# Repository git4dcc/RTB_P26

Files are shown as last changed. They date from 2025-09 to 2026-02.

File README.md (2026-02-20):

# RTB_P26




This is a **motor DCC decoder development board** you can plug right into a breadboard. It has all the necessary hardware for a DCC decoder, except for the microcontroller.

<details>
<summary>See also</summary>

- [RTB_D16](/../../../../git4dcc/RTB_D16) (DCC Decoder)

</details>

<details>
<summary>User Guides</summary>

- User Guide - DE (to be done)
- User Guide - EN (to be done)

</details>

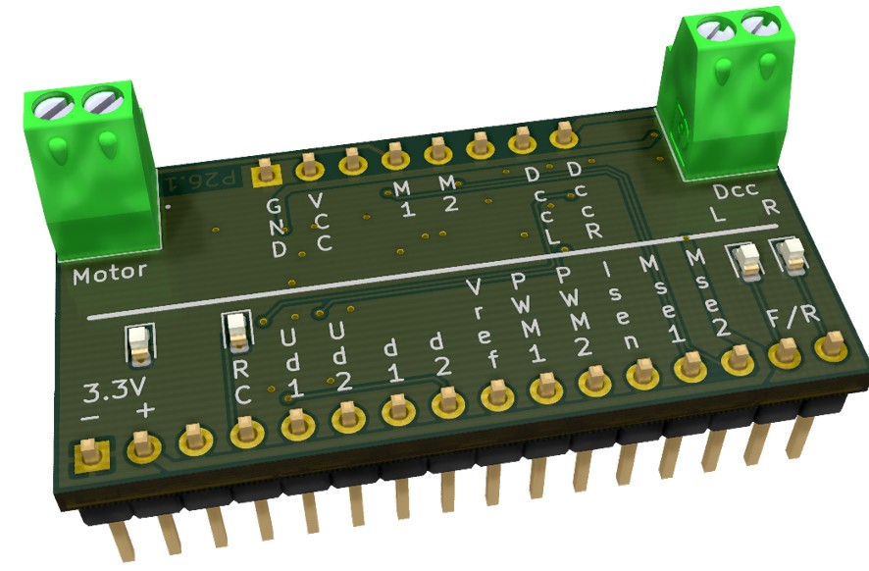
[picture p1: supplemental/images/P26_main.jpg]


# Hardware
My PCB layout uses SMD footprints with mainly 0603 parts. With some experience handsoldering is good to use.

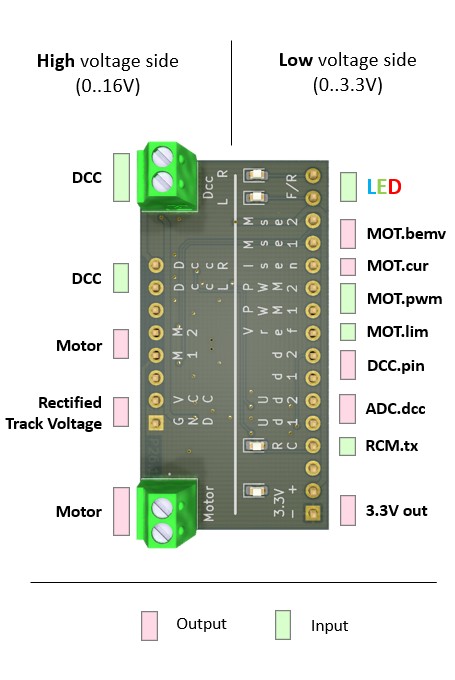
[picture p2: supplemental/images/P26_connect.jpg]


## PCB
- 2-layer PCB, FR4, 1.6mm
- Dimensions: 42mm x 22mm
- VDD voltage: 3.3V, 50mA (optional 5V using a different LDO)
- 18V max DCC voltage
- Railcom transmitter
- Inrush limiter: TPS22810
- H-Bridge: DRV8231

## Kicad
[Schematic](doc/P26_schematic.pdf) | [Layout](doc/P26_layout.pdf) | [Gerber](gerber/P26_0.zip)

<details>
<summary>Dependency</summary>
<br>

:yellow_circle: Requires my Kicad project library [RTB_SamacSys](/../../../../git4dcc/RTB_SamacSys) in the same directory tree.

</details>

# Images
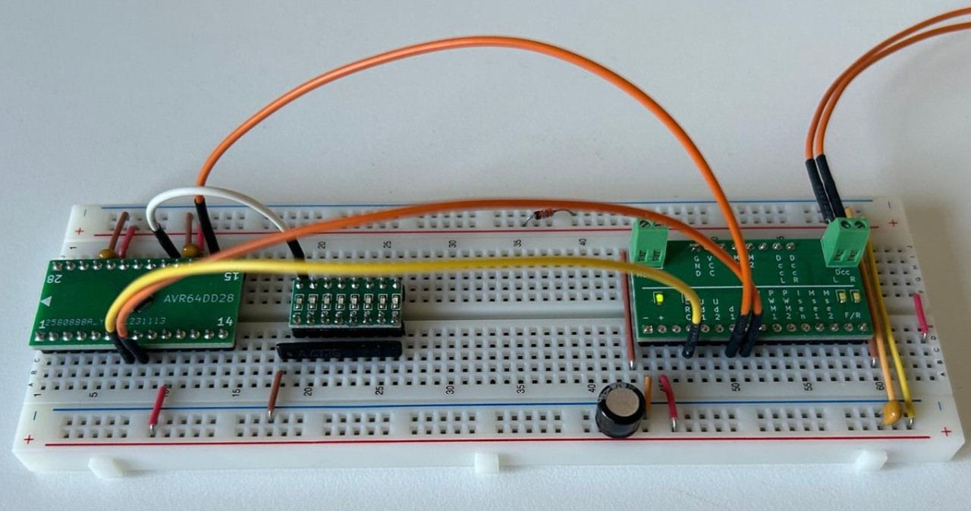
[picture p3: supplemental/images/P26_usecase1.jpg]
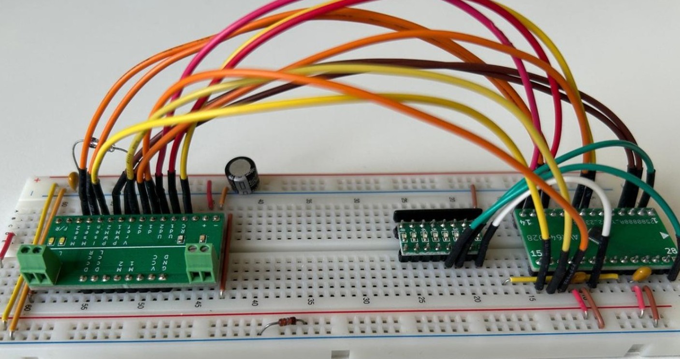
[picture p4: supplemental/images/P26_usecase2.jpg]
 

This project is intended for hobby use only and is distributed in accordance with the Apache License 2.0 agreement.

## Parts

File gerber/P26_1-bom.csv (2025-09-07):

Value | Designator | Footprint | JLCPCB Part# | Description
100n | C2,C4 | Capacitor_SMD:C_0603_1608Metric | C14663 | 100nF 50V X7R ñ10% 0603 Multilayer Ceramic Capacitors MLCC - SMD/SMT ROHS
22u | C3 | Capacitor_SMD:C_0603_1608Metric | C59461 | 22uF 6.3V X5R ñ20% 0603 Multilayer Ceramic Capacitors MLCC - SMD/SMT ROHS
1u | C5,C6 | Capacitor_SMD:C_0603_1608Metric | C15849 | 1uF 50V X5R ñ10% 0603 Multilayer Ceramic Capacitors MLCC - SMD/SMT ROHS
10u | C1,C7 | Capacitor_SMD:C_0603_1608Metric | C96446 | 10uF 25V X5R ñ20% 0603 Multilayer Ceramic Capacitors MLCC - SMD/SMT ROHS
BAS3007ARPPE6327HTSA1 | D1 | BF998215 | C6430958 | 30V 350uA@30V 5A 600mV@700mA 900mA SOT-143 Schottky Diodes ROHS
LED (wht) | D2,D3 | LED_SMD:LED_0603_1608Metric | C2290 | 100mW 120ø 2.6V~3.1V 360mcd 5mA White 0603 LED Indication - Discrete ROHS
LED (blue) | D4 | LED_SMD:LED_0603_1608Metric | C965807 | 120ø 20mA 3.3V 300mcd 455nm~475nm 470nm 70mW Blue Water Clear op View Mount 0603 LED Indication - Discrete ROHS
LED (green) | D5 | LED_SMD:LED_0603_1608Metric | C84264 | -30?~+85? 1.6V~2.6V 13mcd 140ø 25mA 565nm~578nm 576nm 65mW Yellow Green 0603 LED Indication - Discrete ROHS
D_Schottky | D6,D7 | RTB:SM5819L2TP | C3012686 | -40?~+125? 200mA 30uA@30V 3A 40V 480mV@200mA SOD-923F Schottky Diodes ROHS
DRV8231ADSGR | IC1 | SON50P200X200X80-9N | C5139865 | DRV8231: 4.5-V to 33-V, 600-m, shunt
BC847BDW1 | Q1 | Package_TO_SOT_SMD:SOT-363_SC-70-6 | C164103 | -55?~+150? 1 NPN + 1 PNP 100MHz 100mA 15nA 200@2.0mA,5.0V 380mW 45V 600mV@10mA,0.5mA 6V NPN+PNP SOT-363(SC-88) Bipolar (BJT) ROHS
BC857BDW1 | Q2 | Package_TO_SOT_SMD:SOT-363_SC-70-6 | C383198 | -55?~+150? 100MHz 100mA 150@2.0mA,5.0V 15nA 250mW 45V 5V 650mV PNP SOT-363(SC-88) Bipolar (BJT) ROHS
33k | R1,R2 | Resistor_SMD:R_0603_1608Metric | C4216 | -55?~+155? 100mW 33kê 75V Thick Film Resistor ñ1% ñ100ppm/? 0603 Chip Resistor - Surface Mount ROHS
47k | R14,R16 | Resistor_SMD:R_0603_1608Metric | C25819 | -55?~+155? 100mW 47kê 75V Thick Film Resistor ñ1% ñ100ppm/? 0603 Chip Resistor - Surface Mount ROHS
3.3k | R12,R18,R19,R20,R21 | Resistor_SMD:R_0603_1608Metric | C22978 | -55?~+155? 100mW 3.3kê 75V Thick Film Resistor ñ1% ñ100ppm/? 0603 Chip Resistor - Surface Mount ROHS
22 | R3 | Resistor_SMD:R_0603_1608Metric | C23345 | -55?~+155? 100mW 22ê 75V Thick Film Resistor ñ1% ñ100ppm/? 0603 Chip Resistor - Surface Mount ROHS
10k | R4,R5,R10,R11,R15,R17 | Resistor_SMD:R_0603_1608Metric | C25804 | -55?~+155? 100mW 10kê 75V Thick Film Resistor ñ1% ñ100ppm/? 0603 Chip Resistor - Surface Mount ROHS
220k | R6,R7,R13 | Resistor_SMD:R_0603_1608Metric | C22961 | -55?~+155? 100mW 220kê 75V Thick Film Resistor ñ1% ñ100ppm/? 0603 Chip Resistor - Surface Mount ROHS
9.1k | R8,R9 | Resistor_SMD:R_0603_1608Metric | C23260 | -55?~+155? 100mW 75V 9.1kê Thick Film Resistor ñ1% ñ100ppm/? 0603 Chip Resistor - Surface Mount ROHS
TPS22810DRVR | U1 | Package_DFN_QFN:DFN-6-1EP_2x2mm_P0.65mm_EP1x1.6mm | C527679 | -40?~+105? 1 2.7V~18V 3A 79mê Active High Load Switch Undervoltage Protection(UVP) WSON-6-EP(2x2) Power Distribution Switches ROHS
MIC5205-3.3YM5 | U2 | Package_TO_SOT_SMD:SOT-23-5 | C37970 | -40?~+125?@(Tj) 1 150mA 16V 3.3V 350mV@(150mA) 600uA 75dB@(100Hz) Fixed Over Current Protection Positive SOT-23-5 Voltage Regulators - Linear, Low Drop Out (LDO) Regulators ROHS

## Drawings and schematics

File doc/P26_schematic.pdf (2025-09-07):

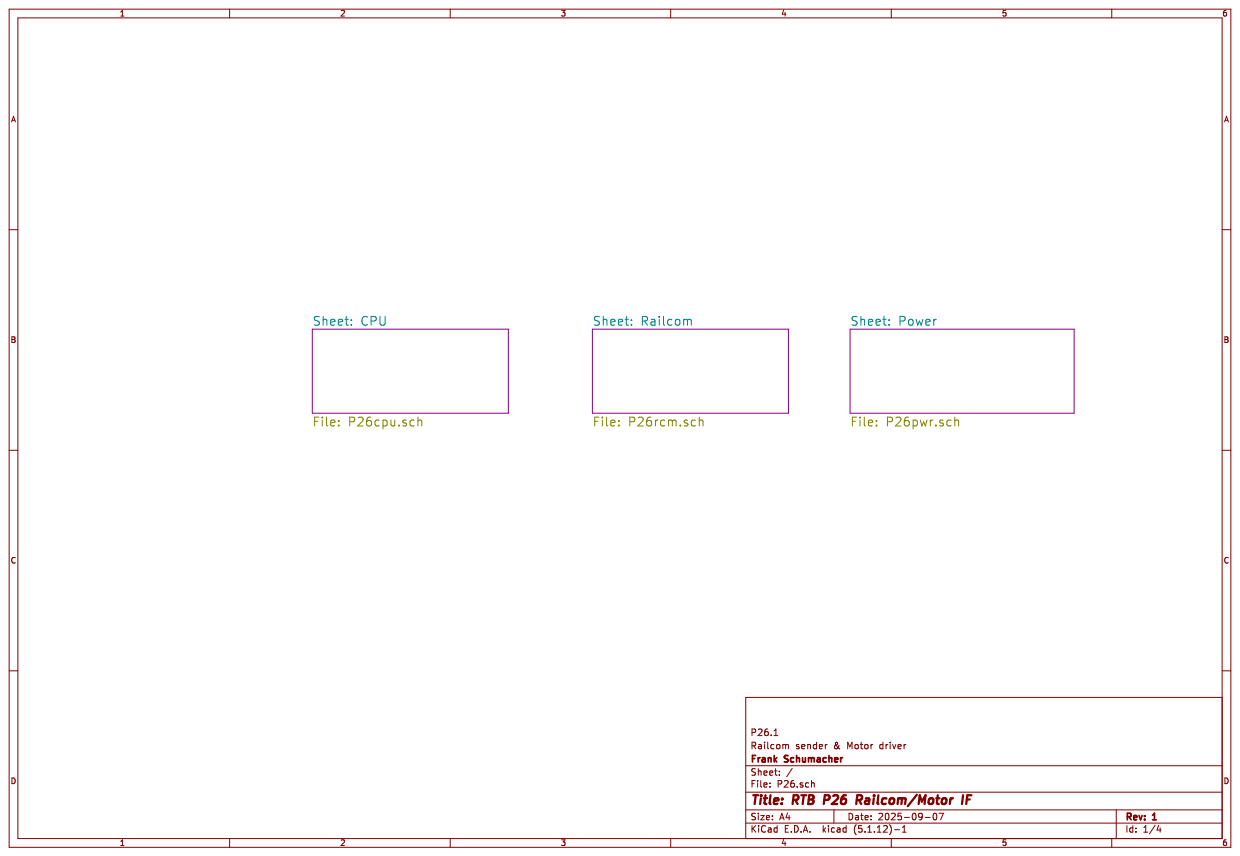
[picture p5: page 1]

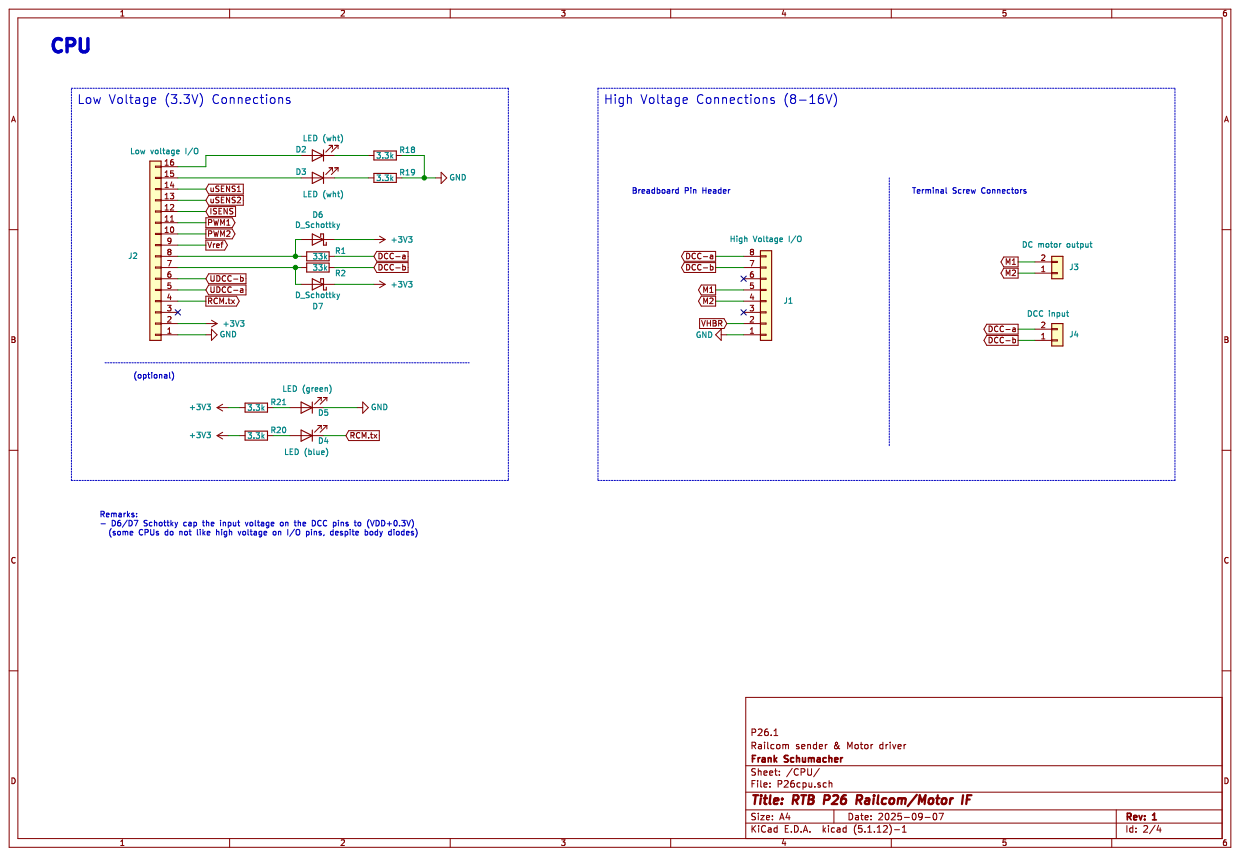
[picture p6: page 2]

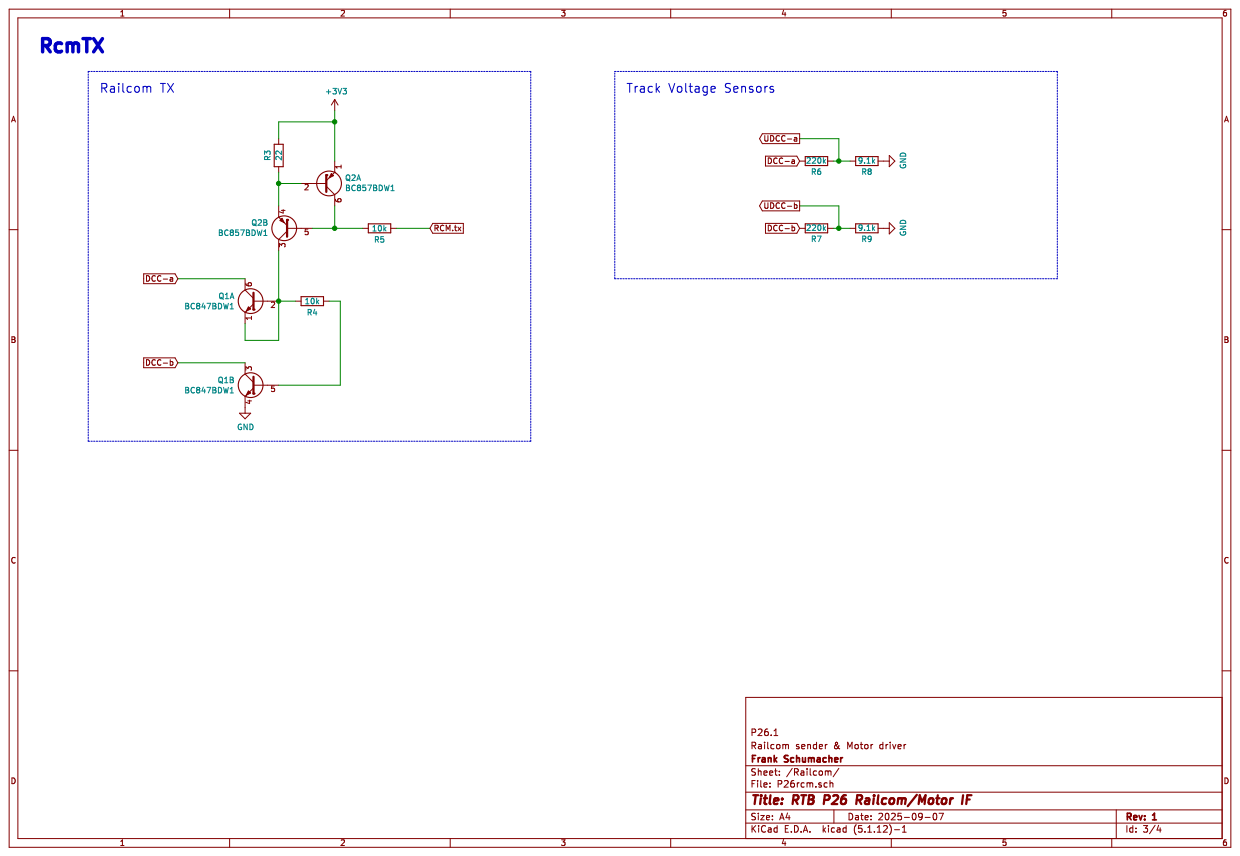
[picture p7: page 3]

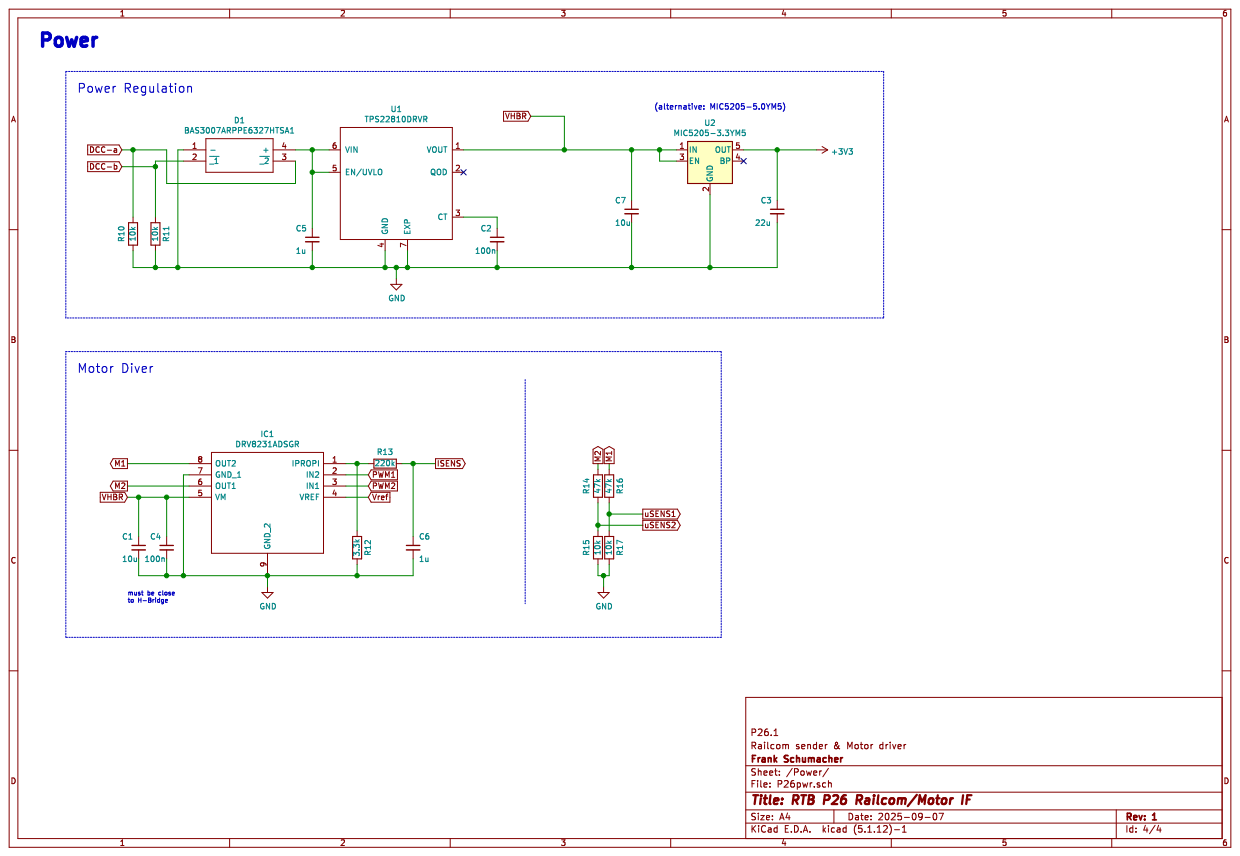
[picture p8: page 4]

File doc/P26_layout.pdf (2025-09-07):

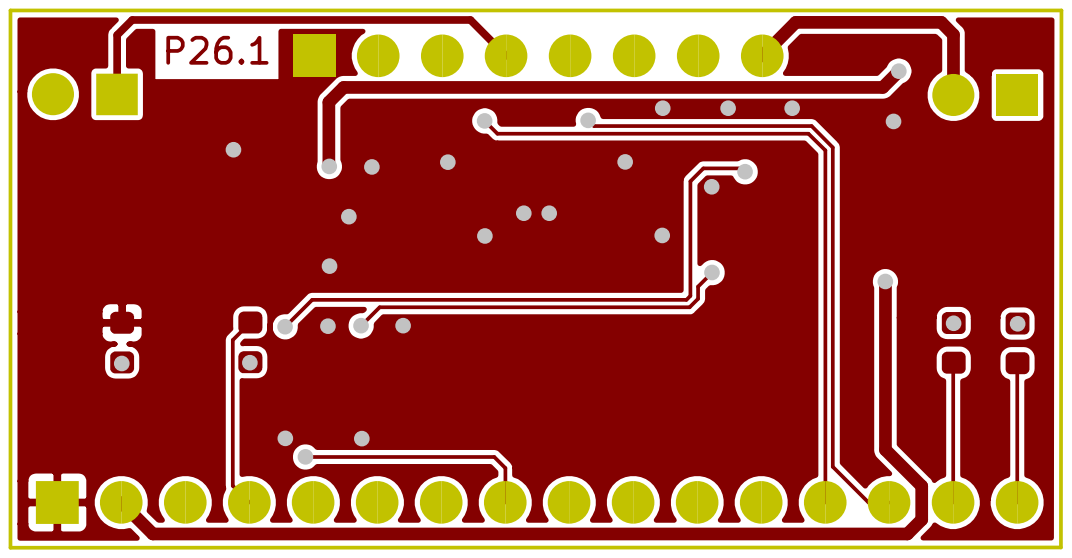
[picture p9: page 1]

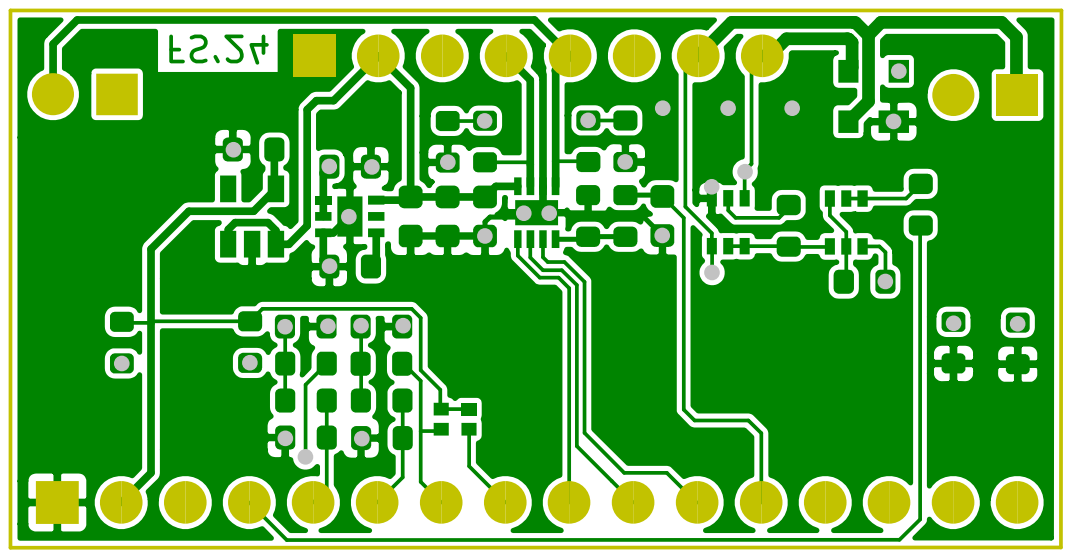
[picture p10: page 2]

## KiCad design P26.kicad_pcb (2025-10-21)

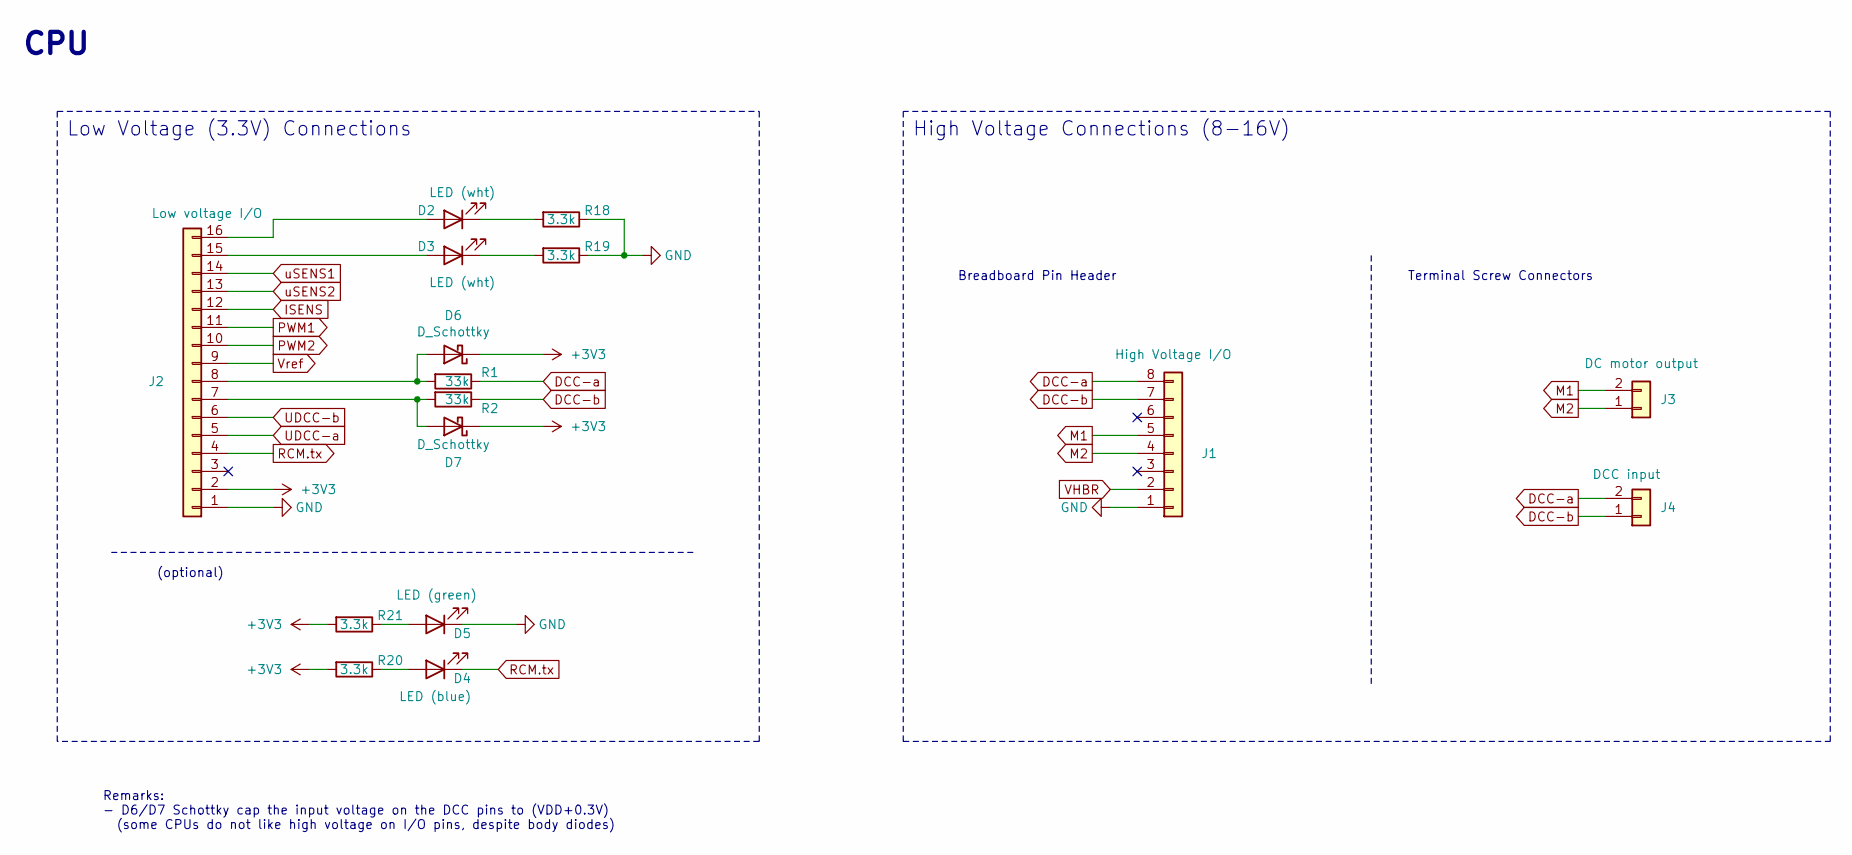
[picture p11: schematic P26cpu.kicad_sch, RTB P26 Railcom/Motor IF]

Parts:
D2, D3: LED (wht); LED_0603_1608Metric; JLCPCB C2290
D4: LED (blue); LED_0603_1608Metric; JLCPCB C965807
D5: LED (green); LED_0603_1608Metric; JLCPCB C84264
D6, D7: D_Schottky; SM5819L2TP; JLCPCB C3012686
J1: High Voltage I/O; PinHeader_1x08_P2.54mm_Vertical
J2: Low voltage I/O; PinHeader_1x16_P2.54mm_Vertical
J3: DC motor output; 1725656
J4: DCC input; 1725656
R1, R2: 33k; R_0603_1608Metric; JLCPCB C4216
R18, R19, R20, R21: 3.3k; R_0603_1608Metric; JLCPCB C22978

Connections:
+3V3: D6.1 (K), D7.1 (K), J2.2, R20.2, R21.2; also elsewhere on the board
DCC-a: J1.8, J4.2, R1.1; also elsewhere on the board
DCC-b: J1.7, J4.1, R2.1; also elsewhere on the board
GND: D5.1 (K), J1.1, J2.1, R18.1, R19.1; also elsewhere on the board
ISENS: J2.12; also elsewhere on the board
M1: J1.5, J3.2; also elsewhere on the board
M2: J1.4, J3.1; also elsewhere on the board
unnamed: D2.2 (A), J2.16
unnamed: D2.1 (K), R18.2
unnamed: D3.2 (A), J2.15
unnamed: D3.1 (K), R19.2
unnamed: D4.2 (A), R20.1
unnamed: D5.2 (A), R21.1
unnamed: D6.2 (A), J2.8, R1.2
unnamed: D7.2 (A), J2.7, R2.2
PWM1: J2.11; also elsewhere on the board
PWM2: J2.10; also elsewhere on the board
RCM.tx: D4.1 (K), J2.4; also elsewhere on the board
UDCC-a: J2.5; also elsewhere on the board
UDCC-b: J2.6; also elsewhere on the board
VHBR: J1.2; also elsewhere on the board
Vref: J2.9; also elsewhere on the board
uSENS1: J2.14; also elsewhere on the board
uSENS2: J2.13; also elsewhere on the board

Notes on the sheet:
CPU
High Voltage Connections (8-16V)
Terminal Screw Connectors
(optional)
Breadboard Pin Header
Low Voltage (3.3V) Connections
Remarks: - D6/D7 Schottky cap the input voltage on the DCC pins to (VDD+0.3V) (some CPUs do not like high voltage on I/O pins, despite body diodes)

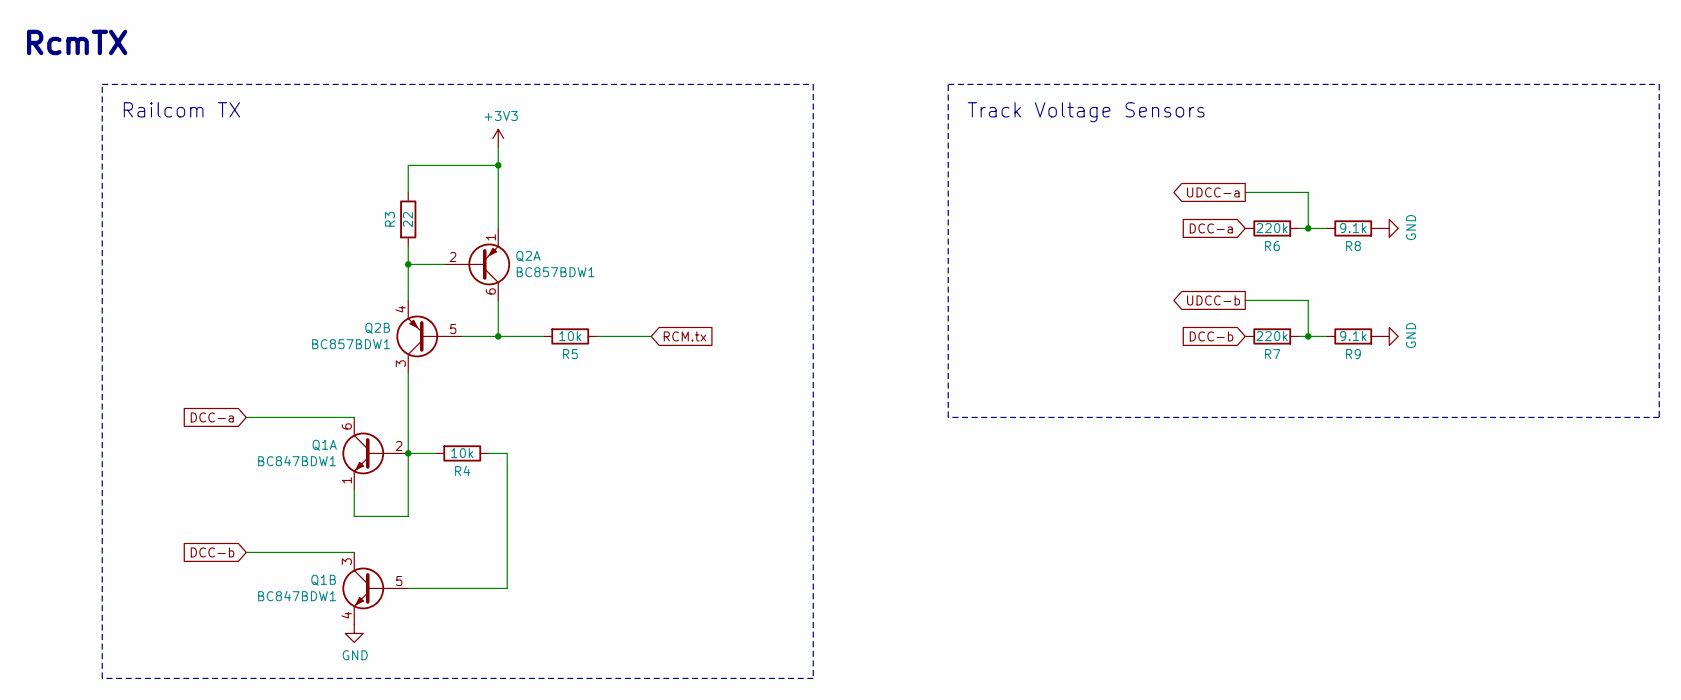
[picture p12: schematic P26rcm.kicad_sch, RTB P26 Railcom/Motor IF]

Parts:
Q1: BC847BDW1; SOT-363_SC-70-6; JLCPCB C164103
Q2: BC857BDW1; SOT-363_SC-70-6; JLCPCB C383198
R3: 22; R_0603_1608Metric; JLCPCB C23345
R4, R5: 10k; R_0603_1608Metric; JLCPCB C25804
R6, R7: 220k; R_0603_1608Metric; JLCPCB C22961
R8, R9: 9.1k; R_0603_1608Metric; JLCPCB C23260

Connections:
+3V3: Q2.1 (E1), R3.1; also elsewhere on the board
DCC-a: Q1.6 (C1), R6.1; also elsewhere on the board
DCC-b: Q1.3 (C2), R7.1; also elsewhere on the board
GND: Q1.4 (E2), R8.2, R9.2; also elsewhere on the board
unnamed: Q1.1 (E1), Q1.2 (B1), Q2.3 (C2), R4.2
unnamed: Q1.5 (B2), R4.1
unnamed: Q2.2 (B1), Q2.4 (E2), R3.2
unnamed: Q2.5 (B2), Q2.6 (C1), R5.2
RCM.tx: R5.1; also elsewhere on the board
UDCC-a: R6.2, R8.1; also elsewhere on the board
UDCC-b: R7.2, R9.1; also elsewhere on the board

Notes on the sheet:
RcmTX
Railcom TX
Track Voltage Sensors

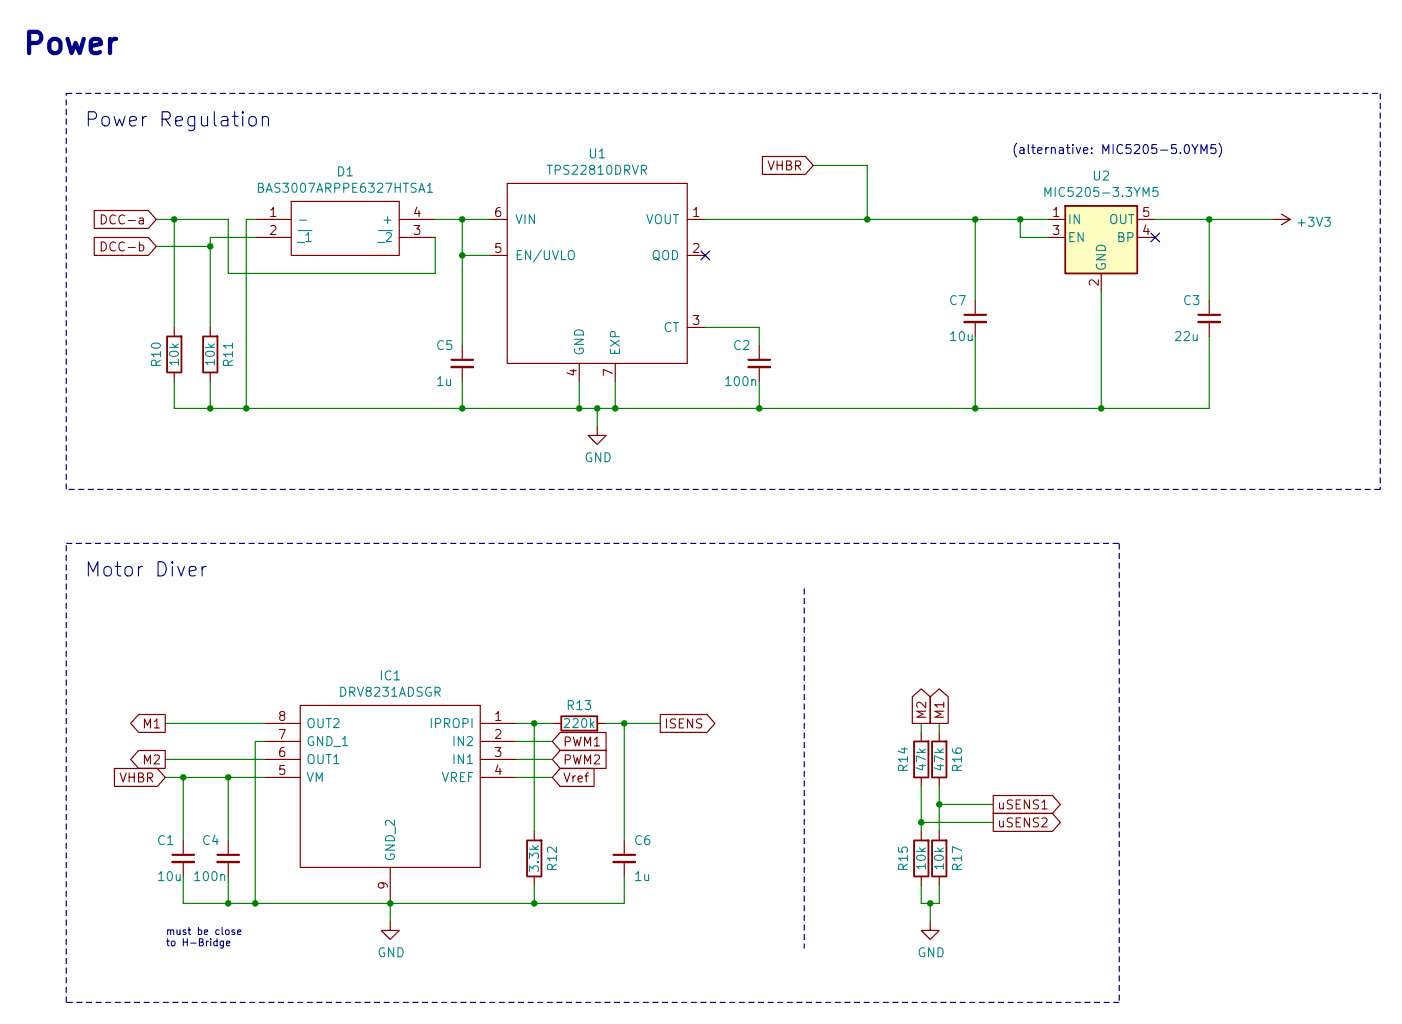
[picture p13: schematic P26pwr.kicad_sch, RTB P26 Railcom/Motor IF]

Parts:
C1, C7: 10u; C_0603_1608Metric; JLCPCB C96446
C2, C4: 100n; C_0603_1608Metric; JLCPCB C14663
C3: 22u; C_0603_1608Metric; JLCPCB C59461
C5, C6: 1u; C_0603_1608Metric; JLCPCB C15849
D1: BAS3007ARPPE6327HTSA1; BF998215; JLCPCB C6430958
IC1: DRV8231ADSGR; SON50P200X200X80-9N; JLCPCB C5139865
R10, R11, R15, R17: 10k; R_0603_1608Metric; JLCPCB C25804
R12: 3.3k; R_0603_1608Metric; JLCPCB C22978
R13: 220k; R_0603_1608Metric; JLCPCB C22961
R14, R16: 47k; R_0603_1608Metric; JLCPCB C25819
U1: TPS22810DRVR; DFN-6-1EP_2x2mm_P0.65mm_EP1x1.6mm; JLCPCB C527679
U2: MIC5205-3.3YM5; SOT-23-5; JLCPCB C37970

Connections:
+3V3: C3.1, U2.5 (OUT); also elsewhere on the board
DCC-a: D1.3 (~_2), R10.2; also elsewhere on the board
DCC-b: D1.2 (~_1), R11.2; also elsewhere on the board
GND: C1.2, C2.2, C3.2, C4.2, C5.2, C6.2, C7.2, D1.1 (-), IC1.7 (GND_1), IC1.9 (GND_2), R10.1, R11.1, R12.1, R15.1, R17.1, U1.4 (GND), U1.7 (EXP), U2.2 (GND); also elsewhere on the board
ISENS: C6.1, R13.2; also elsewhere on the board
M1: IC1.8 (OUT2), R16.2; also elsewhere on the board
M2: IC1.6 (OUT1), R14.2; also elsewhere on the board
unnamed: C5.1, D1.4 (+), U1.5 (EN/UVLO), U1.6 (VIN)
unnamed: IC1.1 (IPROPI), R12.2, R13.1
unnamed: C2.1, U1.3 (CT)
PWM1: IC1.2 (IN2); also elsewhere on the board
PWM2: IC1.3 (IN1); also elsewhere on the board
VHBR: C1.1, C4.1, C7.1, IC1.5 (VM), U1.1 (VOUT), U2.1 (IN), U2.3 (EN); also elsewhere on the board
Vref: IC1.4 (VREF); also elsewhere on the board
uSENS1: R16.1, R17.2; also elsewhere on the board
uSENS2: R14.1, R15.2; also elsewhere on the board

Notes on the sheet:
must be close to H-Bridge
Motor Diver
Power Regulation
Power
(alternative: MIC5205-5.0YM5)

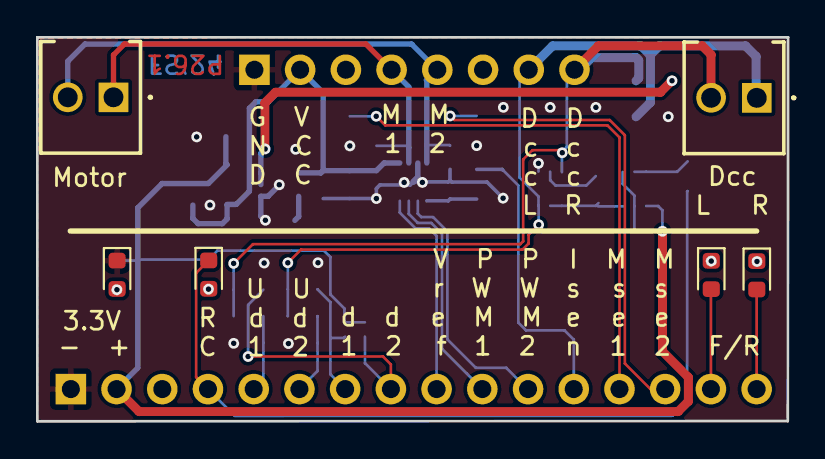
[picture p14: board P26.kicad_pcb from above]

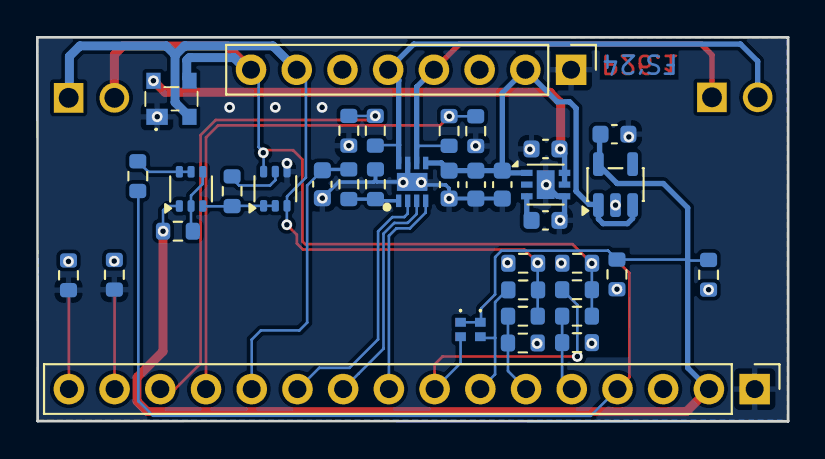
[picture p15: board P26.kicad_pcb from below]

Board: 2 copper layers, 41.7 x 21.3 mm, 44 parts (38 on the bottom side), 31 nets.

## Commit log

2025-09-07 mod: optimized for PCB assembly
    [P26.kicad_pcb, P26.sch, P26cpu.sch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]
2025-10-21 mod: conversion to KiCad 9
    [P26.kicad_pcb, P26.kicad_sch, P26.sch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]
